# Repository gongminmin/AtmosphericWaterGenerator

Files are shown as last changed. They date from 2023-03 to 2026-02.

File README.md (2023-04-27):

# Atmospheric Water Generator



Atmospheric water generator (AWG) is a device for extracting fresh water from air. There are 0.0001% of water exists in the atmosphere. Even the desert air is not completely dry. Extract it for using is better than nothing. If the extraction is carried out near the ocean, where the air humidity is extremely high, the amount of fresh water obtained can be considerable. 

This is a simple open-source AWG design, suitable for home use. We'd like to make it easy to implement, so people can build it at home. The goals are:

* Low building cost. Off-shelve parts as much as possible.
* Easy to duplicate.
* Low operating cost and low power.
* Simple structure and easy maintenance.
* Small size and light weight.
* Safe and reliable.

## Principle

To extract water from air, we need a cold source. It condenses the water out for us to collect. The dry and cold air then be used to cool down the heat from the cold source device.

## Design

We use a [Peltier cooling plate](https://en.wikipedia.org/wiki/Thermoelectric_cooling) as the cold source. It's a solid semiconductor device, no moving part, easy to use. It as a cold side and a hot side. Two water cooling loops are circuiting between the surfaces of cooling plate to radiators. One loop carries the heat from a radiator to the cold side, makes the radiator cold. The other loop carries the heat from hot side to a radiator, exhaust the heat. The condensed water generated from the cold radiator drops down, collected by a bottle. The cooling plate is power consuming. We need a circuit to control it, keeping the temperature of the cold radiator in a certain range.

Most of the components are off-shelve ones. They are mounted to a frame by 3D printed adapters.

## Directories

* 3DModel folder is the 3D model design of some components. It's in STL format, ready for 3D printing.
* Circuit folder is the electric design of the system. The files can be open by [KiCad](https://kicad-pcb.org/)
* Code folder is the Arduino code for the control module.
* Doc folder contains some documents

## License

This project is distributed under the terms of MIT License. See [LICENSE](LICENSE) for details.

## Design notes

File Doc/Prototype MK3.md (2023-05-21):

# Prototype MK3

We simplified the structure a lot in [prototype MK2](Prototype%20MK2.md). Now we need the circuit part.

Let's start with Arduino Mega 2560 and breadboard. First, we connect it with a LCD and a thermistor. With some code, we can measure the temperature.

Thermometer

Then extern the pins of thermistor, add [the code to control](/Code/Control/Control.ino) the temperature into a range. The microcontroller's output is [connected to a MOSFET](/Circuit/AWG.kicad_sch) to turn on/off the cooling plate. Finally, two pumps, two fans, one Arduino are all connected to a 12V power source.

Circuit

In the MK2, the center of gravity is too high. To improve that, we need to reduce the size of the upper platform, so it can fit into the area between the air inlet and outlet. With a [sturdy 3D printed upper platform](/3DModel/UpperPlatform.stl), two water reservoirs and two water pumps can keep close.

Upper Platform

The cooling plate and water blocks are installed into a container, which is then hanging at the bottom of the platform. Note that the room is still not enough for piping. We have to flip the water blocks, make the interface of them pointing to the back.

Cooling Plate

The lower platform is also changed to [3D printed](/3DModel/LowerPlatform.stl) as well. We also used two pipe clamps to fix the pipe onto the platform. To overcome the gap between the clamp and the pipe, 2 layers of soft foam are wrapped around the pipe.

Lower Platform

Now the updated MK3 looks like this.

MK3

## Conclusion

In MK3, with more 3D printed parts, almost all manual works are removed. It's more compact than MK2. The center of gravity is lowered for stability. There is a new problem. The circuit board is too preliminary. And there are still a lot of spots we can use to reduce the size of the device. We'll improve it in the next iteration.

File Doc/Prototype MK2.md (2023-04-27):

# Prototype MK2

The [prototype MK1](Prototype%20MK1.md) has many issues. We need to improve through iteration.

MK1

Firstly, there is a stability problem. This is mainly due to the hard water pipes that generated high stress when bending, cracking open the glue of the water reservoir level. By using specialized right-angle elbow fittings for the bends, and let the pipe run straight.

Elbows

The second problem is too much manual work involved. By using 3D printing, we build [adapters](/3DModel) to mount parts. Most of them has screw holes on sides with a diameter of 4.5mm, which can accommodate imperial #8 or metric M4 screws. The platform is made by medium density fiberboard (MDF), which measures 20x30 centimeters. The water block and the cooling plate are put in a 3D printed [housing](/3DModel/CoolingPlateHousing.stl), attached directly to the platform. The water reservoir has an [adapter](/3DModel/WaterReservoirAdapter.stl), and the water pump has a [baseplate](/3DModel/PumpBaseplate.stl). They are mounted on top of PVC pipes to the upper platform.

UpperPlatform

The heat exchangers are replaced by radiators from water cooling system of computers. Fans are mounted on it, in different facings. The 3D printed adapter reduces the 12cm radiator to 1-1/2-inch pipe. A dust filter can be installed on the inlet side.

Radiators

The pipes are mounted on the lower platform by brackets. The center of the platform has a hole for the tee fitting to go through.

LowerPlatform

Assemble them together, this is our MK2. We use pipes as the frame, MDF as platforms, and 3D printed parts as adapters.

MK2

## Conclusion

In MK2, the only manual work is pipe fitting and drilling. It's much more compact than MK1, with better replicability and stability. Problems in MK1 have been solved. In the next iteration, we'll build the circuit part, and start the overall testing. Also, the barycenter of this device is too high, makes it have the risk of tipping over. It needs to be improved as well.

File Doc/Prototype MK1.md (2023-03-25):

# Prototype MK1

The prototype MK1 is the initial attempt for sorting out the components and the frame. It's basically built from cardboard, fish tank pump, water pipe, etc.

MK1

The top level is the place for two water reservoirs.

TopLevel

The left and right side of the second level are two water pumps. In the middle, two water blocks sandwiching a cooling plate.

2ndLevel

The airflow pipe is built from 1-1/2-inch ABS drainpipe. On the tip, it's a 2 inch to 1-1/2-inch reducer. The two elbow are 60 degree's ones. And a tee fitting is in the middle. Each arm is ~25cm. And in the horizontal section, components are connected by two 4cm pipe.

Pipe

The fan is housed inside a cardboard tube, by iron wires. The tube is 2-inch in diameter, can be mounted to the tip of the pipe.

Fan

Inside each arm, a condenser coil is in place. It's made by wrapping a 3-meter-long refrigerator tube on a 3/4-inch pipe.

Condenser

Unfortunately, the outside diameter of the refrigerator tube is 1/8-inch, but all the rests are in 8mm or 5/16 inch. To connect them, we have to use 5/16 to 3/16 converters, and wrap a thick layer of adhesive tape on the outside of the tube.

Converter

## Conclusion

After the build, there are a lot of problems floating up.

* It's so fragile, easy to break down.
* Too many manual work.
* Big and heavy

In the next iteration, they'll be improved.

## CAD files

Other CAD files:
3DModel/CoolingPlateHousing.stl
3DModel/CoolingPlateHousingSuspension.stl
3DModel/PipeClamp.stl
3DModel/LowerPlatform.stl
3DModel/UpperPlatform.stl
3DModel/PumpBaseplate.stl
3DModel/WaterBottleCap.stl
3DModel/WaterReservoirAdapter.stl
3DModel/RadiatorAdapter.stl
3DModel/PipeAdapter.stl

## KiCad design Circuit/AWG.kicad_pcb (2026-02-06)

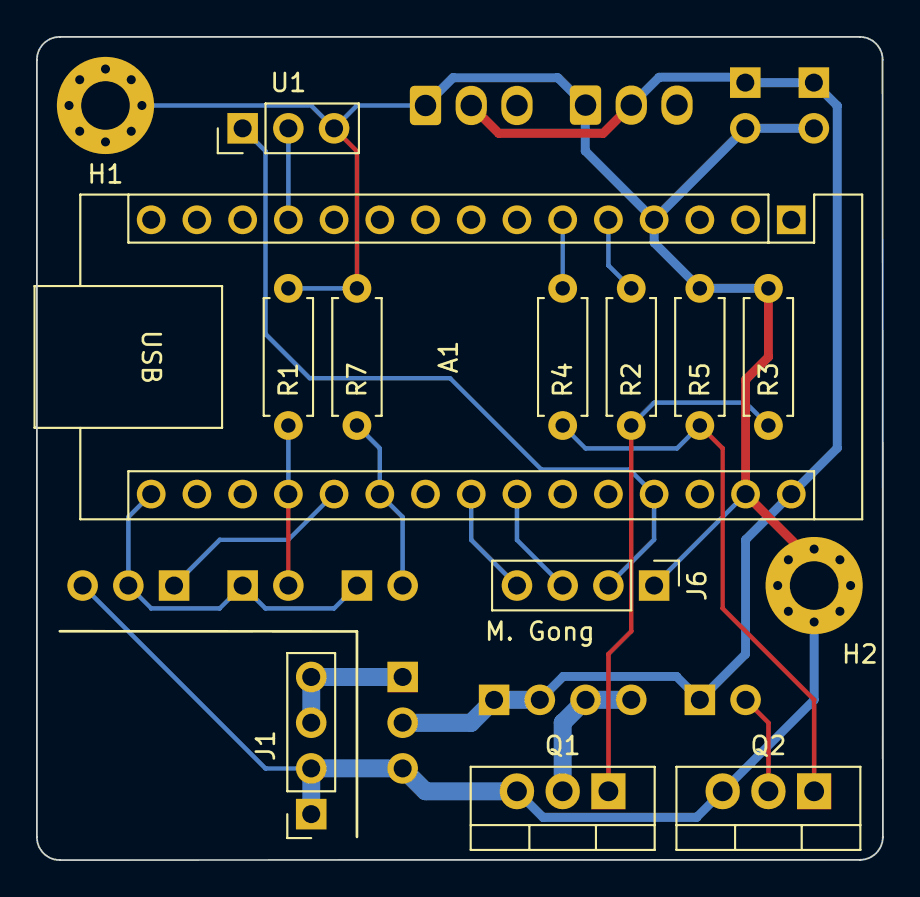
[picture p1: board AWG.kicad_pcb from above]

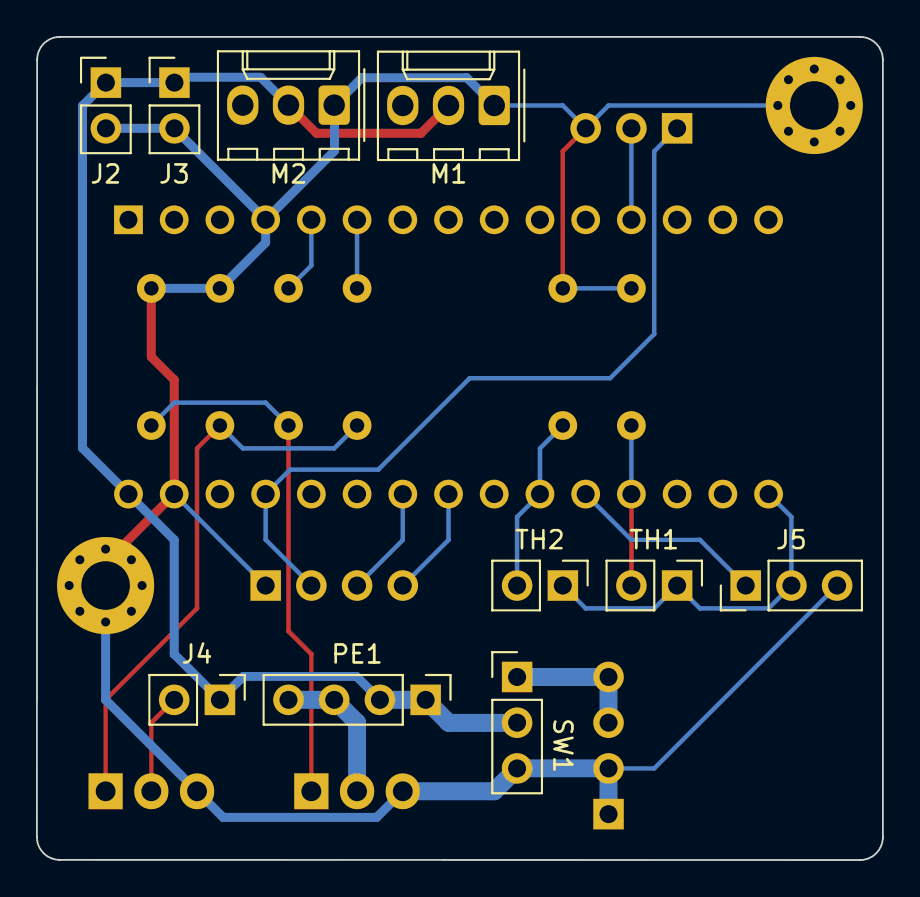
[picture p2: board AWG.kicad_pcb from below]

Board: 2 copper layers, 47.0 x 45.7 mm, 24 parts (10 on the bottom side), 17 nets.

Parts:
A1: Arduino_Nano_v3.x; Arduino_Nano
H1: H1; MountingHole_2.7mm_M2.5_Pad_Via
H2: H2; MountingHole_2.7mm_M2.5_Pad_Via
J1: Power; PinSocket_1x04_P2.54mm_Vertical
J2: Pump 1; PinHeader_1x02_P2.54mm_Vertical
J3: Pump 2; PinHeader_1x02_P2.54mm_Vertical
J4: Pump 3; PinHeader_1x02_P2.54mm_Vertical
J5: WL1; PinHeader_1x03_P2.54mm_Vertical
J6: Display; PinHeader_1x04_P2.54mm_Vertical
M1, M2: Fan_3pin; Molex_KK-254_AE-6410-03A_1x03_P2.54mm_Vertical
PE1: TEC1-12702; PinHeader_1x04_P2.54mm_Vertical
Q1, Q2: RFP30N06LE; TO-220-3_Vertical
R1, R3, R5, R7: 10K; R_Axial_DIN0207_L6.3mm_D2.5mm_P7.62mm_Horizontal
R2, R4: 100; R_Axial_DIN0207_L6.3mm_D2.5mm_P7.62mm_Horizontal
SW1: Switch; PinHeader_1x03_P2.54mm_Vertical
TH1, TH2: 10K; PinHeader_1x02_P2.54mm_Vertical
U1: DHT11; PinHeader_1x03_P2.54mm_Vertical

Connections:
+5V: A1.27 (+5V), J6.2, U1.1
+12V: A1.30 (VIN), J2.1, J3.1, J4.1, M1.2 (+), M2.2 (+), PE1.1, PE1.2, SW1.2
GND: A1.4 (GND), A1.29 (GND), H1.1, H2.1, J1.1, J1.2, J2.2, J3.2, J5.3, J6.1, M1.1 (-), M2.1 (-), Q1.3 (S), Q2.3 (S), R1.2, R3.2, R5.2, R7.2, SW1.3 (K), U1.3
unnamed: A1.19 (A0), R1.1, TH1.2
unnamed: A1.20 (A1), J5.1
unnamed: A1.21 (A2), R7.1, TH2.2
unnamed: A1.23 (A4), J6.4
unnamed: A1.24 (A5), J6.3
unnamed: A1.5 (D2), R2.1
unnamed: A1.6 (D3), R4.2
unnamed: A1.12 (D9), U1.2
unnamed: A1.16 (D13), J5.2, TH1.1, TH2.1
unnamed: J1.3, J1.4, SW1.1
unnamed: J4.2, Q2.2 (D)
unnamed: PE1.3, PE1.4, Q1.2 (D)
unnamed: Q1.1 (G), R2.2, R3.1
unnamed: Q2.1 (G), R4.1, R5.1

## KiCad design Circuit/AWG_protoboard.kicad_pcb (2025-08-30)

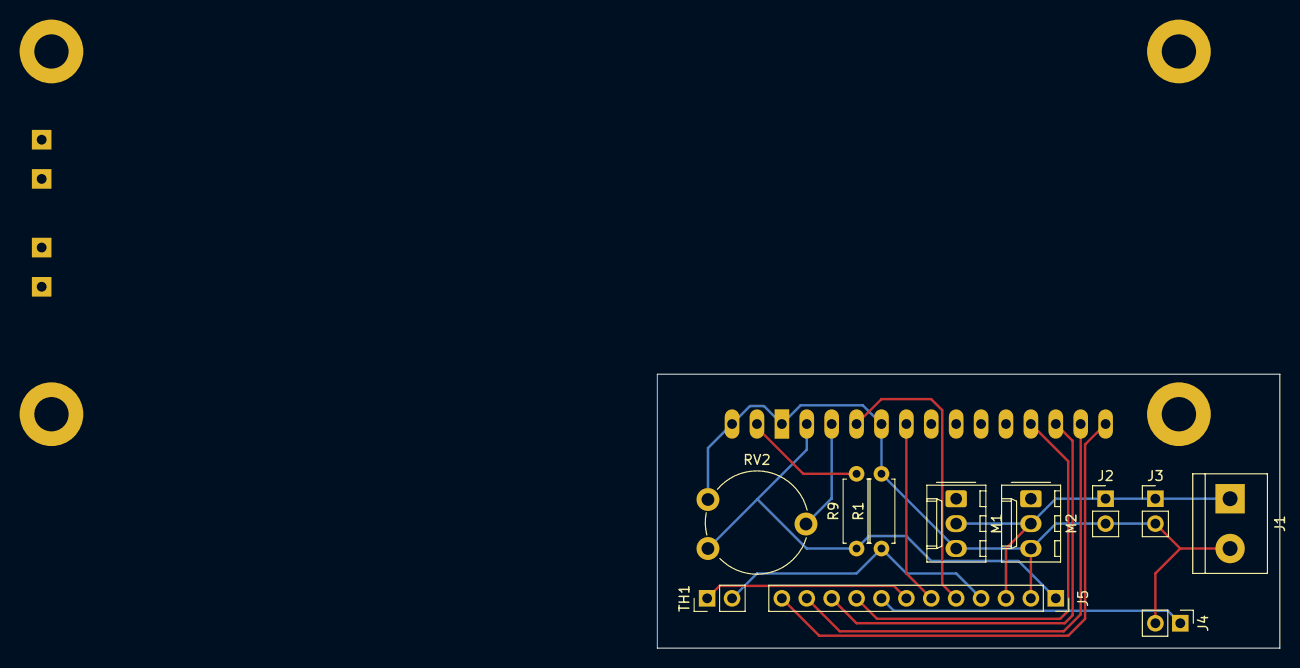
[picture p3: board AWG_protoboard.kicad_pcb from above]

Board: 2 copper layers, 63.5 x 27.9 mm, 12 parts (1 on the bottom side), 14 nets.

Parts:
J1: Power; TerminalBlock_bornier-2_P5.08mm
J2: Pump 1; PinHeader_1x02_P2.54mm_Vertical
J3: Pump 2; PinHeader_1x02_P2.54mm_Vertical
J4: Mosfet; PinHeader_1x02_P2.54mm_Vertical
J5: Arduino; PinSocket_1x12_P2.54mm_Vertical
M1, M2: Fan_3pin; Molex_KK-254_AE-6410-03A_1x03_P2.54mm_Vertical
R1: 10K; R_Axial_DIN0207_L6.3mm_D2.5mm_P7.62mm_Horizontal
R9: 220; R_Axial_DIN0207_L6.3mm_D2.5mm_P7.62mm_Horizontal
RV2: R_Potentiometer; Potentiometer_Piher_PT-10-V10_Vertical
TH1: 10K; PinHeader_1x02_P2.54mm_Vertical
U2: LCD-016N002L

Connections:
+5V: J5.1, R9.1, RV2.1, U2.2 (VDD)
+12V: J1.1, J2.1, J3.1, J5.3, M1.2 (+), M2.2 (+)
/A0: J5.4, R1.1, TH1.2
/D2: J5.12, U2.14 (DB7)
/D3: J5.11, U2.13 (DB6)
/D4: J5.10, U2.12 (DB5)
/D5: J5.9, U2.11 (DB4)
/D6: J4.1, J5.8
/D7: J5.7, TH1.1
/D11: J5.6, U2.6 (E)
/D12: J5.5, U2.4 (RS)
GND: J1.2, J2.2, J3.2, J4.2, J5.2, M1.3 (-), M2.3 (-), R1.2, RV2.3, U2.1 (VSS), U2.5 (R/~W), U2.16 (K)
unnamed: R9.2, U2.15 (A/VEE)
unnamed: RV2.2, U2.3 (VO)

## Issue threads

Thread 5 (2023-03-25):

Improvements on frame

gongminmin, 2023-03-25:
Can we have a 3D printed frame, or we need aluminum extrusion frame.

gongminmin, 2023-05-13:
The 3D printed frame holds well.

Closed 2023-05-13.

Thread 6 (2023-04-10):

Arduino-based control board

gongminmin, 2023-04-10:
Build a circuit board to control the cooling plate.

- [x] Build a temperature sensor
- [x] Enable to control on and off based on temperature
- [x] Connect the control board to the system

Closed 2023-05-03.

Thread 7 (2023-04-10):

Build the power board

gongminmin, 2023-04-10:
12V power for 2 fans, 2 water pumps, and 1 cooling plate. The cooling plate port is controlled by a switch. Others are normally on.

Closed 2023-05-03.

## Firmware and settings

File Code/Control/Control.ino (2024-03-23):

#include <Wire.h>
#include <Adafruit_GFX.h>
#include <Adafruit_SSD1306.h>

#include <DHT.h>

constexpr uint32_t DisplayAddr = 0x3C;

constexpr int TemperatureSensorReadPin = A0;
constexpr int SensorsPowerPin = 13;
constexpr int CoolingPlatePin = 2;

constexpr int DhtPin = 9;

Adafruit_SSD1306& GetDisplay()
{
  constexpr uint32_t ScreenWidth = 128;
  constexpr uint32_t ScreenHeight = 64;
  constexpr int OledReset = -1;

  // Declaration for an SSD1306 display connected to I2C (SDA, SCL pins)
  static Adafruit_SSD1306 display(ScreenWidth, ScreenHeight, &Wire, OledReset);
  return display;
}

DHT& GetDht()
{
  constexpr uint32_t DhtType = DHT11;
  static DHT dht(DhtPin, DhtType);
  return dht;
}

float CalcTemperature(int temperature_sensor)
{
  constexpr float Voltage = 5;
  constexpr int AdcLevels = 1023;
  constexpr int RNominal = 10 * 1000;
  constexpr int Beta = 3950;
  constexpr int RSeries = 10 * 1000;
  constexpr float Kelvin0 = 273.15;
  constexpr float TNominal = 25 + Kelvin0;

  float vi = temperature_sensor * (Voltage / AdcLevels);
  float r = (Voltage - vi) * RSeries / vi;
  float temperature =  1 / (1 / TNominal + log(r / RNominal) / Beta) - Kelvin0;

  constexpr int HistoryLength = 8;
  static float temperature_history[HistoryLength];
  static int temperature_history_size = 0;
  static int temperature_history_write_index = 0;

  temperature_history[temperature_history_write_index] = temperature;
  temperature_history_write_index = (temperature_history_write_index + 1) % HistoryLength;
  temperature_history_size = min(temperature_history_size + 1, HistoryLength);

  float avg = 0;
  for (uint32_t i = 0; i < temperature_history_size; ++i)
  {
    avg += temperature_history[i];
  }
  avg /= temperature_history_size;

  return avg;
}

bool TriggerState(float value, float lower_bound, float upper_bound, bool curr_state)
{
  if (curr_state)
  {
    if (value <= lower_bound)
    {
      curr_state = false;
    }
  }
  else
  {
    if (value > upper_bound)
    {
      curr_state = true;
    }
  }

  return curr_state;
}

void setup()
{
  Adafruit_SSD1306& display = GetDisplay();
  DHT& dht = GetDht();

  Serial.begin(9600);
  if (!display.begin(SSD1306_SWITCHCAPVCC, DisplayAddr)) {
    Serial.println("SSD1306 allocation failed");
    for (;;)
    {
    }
  }

  dht.begin();

  display.clearDisplay();
  display.setTextSize(1);
  display.setTextColor(WHITE);
  display.dim(true);
  display.display();

  pinMode(CoolingPlatePin, OUTPUT);
  digitalWrite(CoolingPlatePin, LOW);

  pinMode(SensorsPowerPin, OUTPUT);
  digitalWrite(SensorsPowerPin, LOW);
}

void loop()
{
  Adafruit_SSD1306& display = GetDisplay();
  DHT& dht = GetDht();

  digitalWrite(SensorsPowerPin, HIGH);
  delay(10);

  int temperature_sensor = analogRead(TemperatureSensorReadPin);

  digitalWrite(SensorsPowerPin, LOW);

  float temperature = CalcTemperature(temperature_sensor);

  display.clearDisplay();

  display.setCursor(0, 8);
  display.print("Cold");
  display.setCursor(0, 16);
  display.print(temperature);
  display.print(static_cast<char>(247));
  display.print("C");
  display.setCursor(0, 24);
  display.print(millis() / 1000.0f, 1);

  constexpr float TemperatureLowerBound = 14;
  constexpr float TemperatureUpperBound = TemperatureLowerBound + 5;
  static bool cooling_plate_on = false;
  cooling_plate_on = TriggerState(temperature, TemperatureLowerBound, TemperatureUpperBound, cooling_plate_on); 
  digitalWrite(CoolingPlatePin, cooling_plate_on ? HIGH : LOW);

  if (cooling_plate_on)
  {
    display.setCursor(108, 32);
    display.print('C');
  }

  float env_temperature = dht.readTemperature();
  float env_humidity = dht.readHumidity();
  if (!isnan(env_humidity) && !isnan(env_temperature)) {
    display.setCursor(64, 8);
    display.print("Env");
    display.setCursor(64, 16);
    display.print(env_temperature, 1);
    display.print(static_cast<char>(247));
    display.print("C");
    display.setCursor(64, 24);
    display.print(round(env_humidity));
    display.print("%");
  }

  display.display();

  delay(500);
}

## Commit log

2023-03-25 Add 3D models of adapters
    [CoolingPlateHousing.stl, CoolingPlateHousingStrip.stl, PipeAdapter.stl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]
2023-03-25 Add circuit design
    [AWG.kicad_sch]
2023-03-25 Add document for prototype MK1
    Related issue: #1
2023-04-04 [Model] Add pipe spacer model, and update the water bottle cap model
    [PipeSpacer.stl, WaterBottleCap.stl]
2023-04-10 [Doc] Add document for prototype MK2
    Related issue: #2
    [CoolingPlateHousingBaffle.stl, PumpBaseplate.stl, WaterReservoirAdapter.stl]
2023-04-10 [Circuit] Change a resistor to a potentiometer to adjust upper bound of the switching
    [AWG.kicad_sch]
2023-04-27 [Code] Add test code for temperature measuring
    Related issue #6
2023-04-27 [Circuit] Redesign the control module, use an Arduino as the computation core
    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
    [AWG.kicad_sch]
2023-05-01 [Circuit] Adjust the mosfet part in the circuit
    [AWG.kicad_sch]
2023-05-01 [Circuit] Import the footprint of heat sink
2023-05-02 [Circuit] Connect sensors to a digital output pin of the Arduino
    [AWG.kicad_sch]
2023-05-02 [Code] Add temperature range control code
    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
    [Control.ino]
2023-05-03 [Circuit] Fix the NTC symbol
    [AWG.kicad_sch]
2023-05-13 [3DModel] 3D printed upper and lower frames
    Related issue #5
    [CoolingPlateHousing.stl, CoolingPlateHousingBaffle.stl, LowerPlatform.stl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]
2023-05-21 [Doc] Add document for prototype MK3
2024-02-05 [Circuit] Remove the unnecessary heatsinks
    [AWG.kicad_sch]
2024-02-06 [Circuit] Simplify the water level sensor to a connector
    [AWG.kicad_sch]
2024-02-10 [Circuit] Add protoboard design
    [AWG_protoboard.kicad_pcb, AWG_protoboard.kicad_sch]
2024-02-17 [Circuit] Improvements on protoboard layout
    [AWG_protoboard.kicad_pcb, AWG_protoboard.kicad_sch]
2024-02-28 [Circuit] Change to use I2C screen
    [AWG.kicad_sch]
2024-03-01 [Circuit] Switch to Arduino Nano
    [AWG.kicad_sch]
2024-03-04 [Code] Improve the text on display
    * Increase the font size.
    * Drop the loop frequency to 2Hz.
2024-03-04 [Circuit] Adjust footprints and references
    [AWG.kicad_sch]
2024-03-04 [Code] Add cooling plate status to display
2024-03-12 [Circuit][Code] Add a DHT module to measure environment temperature and humidity
    [AWG.kicad_sch]
2024-03-22 [3DModel] Update the cooling plate housing design
    [CoolingPlateHousing.stl, CoolingPlateHousingBaffle.stl, CoolingPlateHousingSuspension.stl]
2024-03-23 [Circuit] Adjust the GPIOs and design a PCB
    [AWG.kicad_pcb, AWG.kicad_sch]
2025-08-30 [Circuit] Upgrade to KiCAD 9
    [AWG.kicad_pcb, AWG.kicad_sch, AWG_protoboard.kicad_pcb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]
2025-08-31 [Circuit] Fix symbol warnings
    [AWG.kicad_sch]
2026-02-06 [Circuit] Update the footprints
    [AWG.kicad_pcb, AWG.kicad_sch]
